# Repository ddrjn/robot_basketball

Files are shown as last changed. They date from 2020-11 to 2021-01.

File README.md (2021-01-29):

stm32 based board design and firmware for robot basketball

Tu run the codes you need processing environment, download from processing.org
 Then add libraries from library manager, only one needed to add is processing.video
Connect camera and stm board. 
Press run. 
One code is for serial communication and keyboard controll.
One is for camera and serial comunication
Last one is for webserver setub and webcontrol of robot.

For mainboard firmware there is main.c file. It is meant for stm cube ide
Configure the stm board as described on wiki and paste the main.c code in there.

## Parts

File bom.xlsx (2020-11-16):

Name | Part Name | Footprint | Quantity | Manufacturer | Supplier | Supplier part ID | Link
reverse voltage protection mosfet | BUK6Y10-30PX | LFPAK56 | 1 | NEXPERIA | fernell | 3438512 | https://ee.farnell.com/nexperia/buk6y10-30px/mosfet-p-ch-30v-80a-lfpak56/dp/3438512?st=buk6y10-30px
zener diode | MMSZ5234BT1G | SOD-123 | 1 |  | fernell | 1431276 | https://ee.farnell.com/on-semiconductor/mmsz5234bt1g/diode-zener-6-2v-0-5w/dp/1431276?st=mmsz5234b
5 v regulator | TPS70950DBVR | SOT-23-5 | 1 |  | fernell | 3122409 | https://ee.farnell.com/texas-instruments/tps70950dbvr/ldo-fixed-0-15a-5v-sot-23-5/dp/3122409?st=tps70950
motor driver | DRV8874QPWPRQ1 |  | 3 |  | mouser | 595-DRV8874QPWPRQ1 | https://www.mouser.ee/ProductDetail/Texas-Instruments/DRV8874QPWPRQ1?qs=mAH9sUMRCttZUT1myh3Itg==
isolator- 16pin | SI8660BB-B-IU | QSOP | 1 | silicon labs | fernell | 3105912 | https://ee.farnell.com/silicon-labs/si8660bb-b-iu/digital-isolator-6ch-40-to-125deg/dp/3105912
isolator 8pin | SI8620BB-B-IS | qsop | 1 | silicon labs | fernell | 2423240 | https://ee.farnell.com/silicon-labs/si8620bb-b-is/digital-isolator-8ns-nsoic-8/dp/2423240
usb connector | 10118193-0001LF | TH | 1 |  | fernell | 2751675 | https://ee.farnell.com/amphenol-icc-fci/10118193-0001lf/micro-usb-2-0-type-b-rcpt-smt/dp/2751675?ost=2751675
esd protection | USBLC6-2SC6 | sot23 | 1 |  | fernell | 1269406 | https://ee.farnell.com/stmicroelectronics/usblc6-2sc6/esd-protection-3-5pf-17v-sot23/dp/1269406?st=usblc6-2sc6
programmer connector | FTSH-105-01-L-DV-K-P | SM | 1 |  | fernell | 2856437 | https://ee.farnell.com/samtec/ftsh-105-01-l-dv-k-p/connector-header-10pos-2row-1/dp/2856437
microprocessor | STM32G431KBT6 | LQFP-32 | 1 | STM | mouser | 511-STM32G431KBT6 | https://www.mouser.ee/ProductDetail/STMicroelectronics/STM32G431KBT6?qs=T3oQrply3y8teCTeNAFOLg%3D%3D | fernell appears to have them only from december
connector for motors | 215079-4 |  | 5 |  | fernell | 1772996 | https://ee.farnell.com/amp-te-connectivity/215079-4/connector-4way-vertical-1-27/dp/1772996
3.3v regulator | TLV70233DBVR | SOT-23-5 | 1 |  | fernell | 3007784 | https://ee.farnell.com/texas-instruments/tlv70233dbvr/ldo-fixed-3-3v-0-3a-sot-23-5/dp/3007784?ost=3007784

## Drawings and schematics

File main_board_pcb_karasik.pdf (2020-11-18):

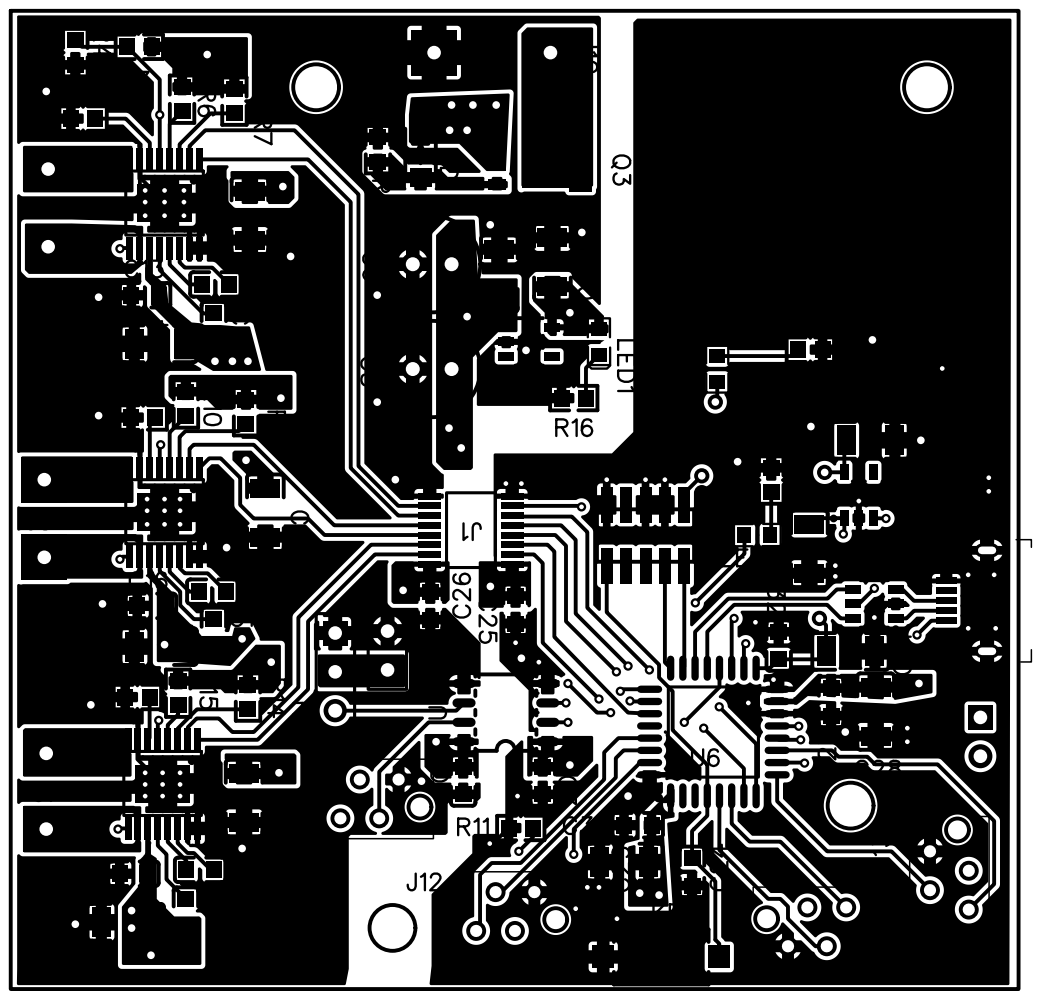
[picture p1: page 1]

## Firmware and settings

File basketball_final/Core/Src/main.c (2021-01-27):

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
/* Includes ------------------------------------------------------------------*/
#include "main.h"
#include "usb_device.h"
#include "usbd_cdc_if.h"
#include "stdio.h"
#include "stdlib.h"
#include "string.h"
#include "Math.h"
/* USER CODE BEGIN Includes */
int tv=0;
/* USER CODE END Includes */

TIM_HandleTypeDef htim1;
TIM_HandleTypeDef htim2;
TIM_HandleTypeDef htim3;
TIM_HandleTypeDef htim8;
TIM_HandleTypeDef htim15;
TIM_HandleTypeDef htim17;

void SystemClock_Config(void);
static void MX_GPIO_Init(void);
static void MX_TIM1_Init(void);
static void MX_TIM2_Init(void);
static void MX_TIM3_Init(void);
static void MX_TIM8_Init(void);
static void MX_TIM15_Init(void);
static void MX_TIM17_Init(void);
/* USER CODE BEGIN 0 */
typedef struct Command { // (1)
  int16_t speed1;
  int16_t speed2;
  int16_t speed3;
  uint16_t throwerSpeed;
  uint16_t delimiter; // (2)
} Command;

typedef struct Feedback { // (3)
  int16_t speed1;
  int16_t speed2;
  int16_t speed3;
  uint16_t delimiter;
} Feedback;

char* rec;

uint8_t usbuf[100];
uint8_t lastlen=100;

Command command = {.speed1 = 0, .speed2 = 0, .speed3 = 0, .throwerSpeed = 0, .delimiter = 0}; // (4)
volatile uint8_t isCommandReceived = 0; // (5)

void CDC_On_Receive(uint8_t* buffer, uint32_t* length) { // (6)
  //if (*length == sizeof(Command)) { // (7)
	uint8_t len1=(uint8_t) *length;
	lastlen=len1;
	memset(usbuf, "\0",100);
   memcpy(usbuf, buffer, len1);
	memset(buffer, "\0",100);
   // (8)
    //memcpy(&rec, buffer, 200);
   // if (command.delimiter == 43690) { // (9)
      isCommandReceived = 1;
   // }
 //}
}




uint8_t ret[9][5];
int m2s=0;
uint16_t values[9];
//m1speed,m2speed,m3speed,m1dir,m2dir,m3dir,servo1,servo2,esc


void splitm(uint8_t* msg){

  for (int i=0;i<9;i++){

      values[i]=0;

  }


int count=0;
int mpov=-1;


  for (int i=0;i<lastlen;i++){


    if(msg[i]==';'){int mpov1=mpov;
      while(mpov!=-1){
        values[count]+=(ret[count][mpov1-mpov]-48)*pow(10,mpov);
        mpov--;


      }

      count++; mpov=-1;}

    else{


      mpov++;
      ret[count][mpov]=msg[i];

    }



//    if(msg[i]==';'){ret[0]=10;break;}
//    if(msg[i]==','){ret[0]=50;break;}
//    if(msg[i]==':'){ret[0]=100;break;}
//    if(msg[i]=='|'){ret[0]=0;break;}

  }









}





uint16_t fdbck;



/* USER CODE END 0 */

/**
  * @brief  The application entry point.
  * @retval int
  */
int main(void)
{
  /* MCU Configuration--------------------------------------------------------*/

  /* Reset of all peripherals, Initializes the Flash interface and the Systick. */
  HAL_Init();

  /* Configure the system clock */
  SystemClock_Config();

  /* Initialize all configured peripherals */
  MX_GPIO_Init();
  MX_USB_Device_Init();
  MX_TIM1_Init();
  MX_TIM2_Init();
  MX_TIM3_Init();
  MX_TIM8_Init();
  MX_TIM15_Init();
  MX_TIM17_Init();
  /* Infinite loop */
  /* USER CODE BEGIN WHILE */


  MX_TIM15_Init();//m1en and m2en
  MX_TIM8_Init();//m3en

  MX_TIM3_Init();//servo2 channel 2
  HAL_TIM_PWM_Start(&htim15, TIM_CHANNEL_2);//m1
  HAL_TIM_PWM_Start(&htim15, TIM_CHANNEL_1);//m2
  HAL_TIM_PWM_Start(&htim8, TIM_CHANNEL_1);//m3
  HAL_TIM_PWM_Start(&htim3, TIM_CHANNEL_2);//servo
  HAL_TIM_PWM_Start(&htim2, TIM_CHANNEL_4);//esc
  HAL_TIM_PWM_Start(&htim3, TIM_CHANNEL_3);//esc


  HAL_GPIO_WritePin(GPIOA, GPIO_PIN_9, GPIO_PIN_SET);
  HAL_GPIO_WritePin(GPIOA, GPIO_PIN_5, GPIO_PIN_SET);
  HAL_GPIO_WritePin(GPIOB, GPIO_PIN_4, GPIO_PIN_SET);






  while (1)
  {
    /* USER CODE END WHILE */

    /* USER CODE BEGIN 3 */


	  if (isCommandReceived) { // (2)
	        isCommandReceived = 0;
	        HAL_GPIO_TogglePin(GPIOB,GPIO_PIN_3); // (3)



	      splitm(usbuf);//allocate values sent from pc to values variable

	      //phase of M1
	      if(values[3]==1)HAL_GPIO_WritePin(GPIOA, GPIO_PIN_9, GPIO_PIN_SET);
	      	  	  else if(values[3]==0)GPIOA -> ODR &= ~GPIO_PIN_9;
	      //phase of M2
	      if(values[4]==1)HAL_GPIO_WritePin(GPIOA, GPIO_PIN_5, GPIO_PIN_SET);
	     	      else if(values[4]==0)GPIOA -> ODR &= ~GPIO_PIN_5;
	      //phase of M3
	      if(values[5]==1)HAL_GPIO_WritePin(GPIOB, M3PH_Pin, GPIO_PIN_SET);
	     	      else if(values[5]==0)GPIOB -> ODR &= ~M3PH_Pin;




	        TIM15->CCR2 = values[0];//M1EN
	          TIM15->CCR1 = values[1];//M2En
	          TIM8->CCR1 = values[2];//M3EN





              //11111;11111;11111;1;1;1;1000;1000;99999 test transmition
//servo and esc receive values from 0-10000, motors from 0 - 65535
int servod=values[6];
servod=(int)servod/1.574;
servod=servod+1640;

	TIM3->CCR2 = servod;//servo2





int escs=values[7];
if(escs!=0){
escs=(int)escs/3.335;
escs=escs+3500;

//
TIM2->CCR4 = escs;//esc
	TIM3->CCR3 = escs;//esc


}

	       //CDC_Transmit_FS(values, sizeof(values)); // (5)

	      }

  }
  /* USER CODE END 3 */
}

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


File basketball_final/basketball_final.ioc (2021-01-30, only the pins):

Mcu.UserName=STM32G431KBTx
PA10.Signal=S_TIM2_CH4
PA11.Signal=USB_DM
PA12.Signal=USB_DP
PA13.Signal=SYS_JTMS-SWDIO
PA14.Signal=SYS_JTCK-SWCLK
PA15.GPIO_Label=TIM8_CH1_M3EN
PA15.Signal=S_TIM8_CH1
PA2.GPIO_Label=TIM15_CH1_M2EN
PA2.Signal=S_TIM15_CH1
PA3.GPIO_Label=TIM15_CH2_M1EN
PA3.Signal=S_TIM15_CH2
PA5.GPIO_Label=M2PH
PA5.Signal=GPIO_Output
PA7.Signal=S_TIM3_CH2
PA8.GPIO_Label=TIM1_CH1_SERVO1
PA8.Signal=S_TIM1_CH1
PA9.GPIO_Label=M1PH
PA9.Signal=GPIO_Output
PB0.Signal=S_TIM3_CH3
PB3.GPIO_Label=MCU_LED
PB3.Signal=GPIO_Output
PB4.GPIO_Label=M3PH
PB4.Signal=GPIO_Output

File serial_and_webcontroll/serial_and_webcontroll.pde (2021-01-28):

/**
 * Simple Write. 
 * 
 * Check if the mouse is over a rectangle and writes the status to the serial port. 
 * This example works with the Wiring / Arduino program that follows below.
 */


import processing.serial.*;
import processing.net.*;

Server s;
Client c;
Serial myPort;  // Create object from Serial class
int val;        // Data received from the serial port
int s1,s2,s3,d1,d2,d3,servo,esc;
int data[];
void setup() 
{
  size(200, 200);
  // I know that the first port in the serial list on my mac
  // is always my  FTDI adaptor, so I open Serial.list()[0].
  // On Windows machines, this generally opens COM1.
  // Open whatever port is the one you're using.
  String portName = Serial.list()[0];
  myPort = new Serial(this, portName, 115200);
  s = new Server(this, 12345);
  s1=1000;
  s2=1000;
  d3=1;

}

void draw() {
  background(255);
 
       c = s.available();
  if (c != null) {
    String input = c.readString();
    input = input.substring(0, input.indexOf("\n")); // Only up to the newline
    data = int(split(input, ',')); // Split values into an array
    // Draw line using received coords
   s1=data[0];
    s2=data[1];
     s3=data[2];
      d1=data[3];
    d2=data[4];
     d3=data[5];
      servo=data[6];
   esc=data[7];
   
       
  myPort.write(generateMessage()); 
     
   
   
  }
      
      
      
      
      

}


void mousePressed(){
  
  //moveF(10000);
  //turn(1,10000);
}


void keyPressed(){
  
 if(key=='w'){
 moveF(40000,1);
 
 } 
   if(key=='a'){
turn(1,10000);
 
 } 
    if(key=='d'){
turn(0,10000);
 
 } 
  
      if(key=='s'){
moveF(10000,0);
 
 } 
  
  
}


void keyReleased(){
  
  
 stopM(); 
  
}
void mouseReleased(){
  
 stopM(); 
  //turn(0,20000);
  
}

void moveF(int speed,int dir){
  d1=0;
  d2=1;
  if(dir==0){d1=1;d2=0;}
  
  s3=0;
  s1=speed;
  s2=speed;
  
  
  
  
  
  myPort.write(generateMessage());     
  
  
  
}


void stopM(){
s1=0;
s2=0;
s3=0;

 myPort.write(generateMessage());     

}


void turn(int dir,int speed){
  if (dir==1){
   d1=1;
   d2=1;
   d3=1;
    
    
  }
  else {
     d1=0;
   d2=0;
   d3=0;
   
  }
  s1=speed;
  s2=speed;
  s3=speed;
  
  
  myPort.write(generateMessage());     
  
  
  
  
}


String generateMessage(){
  
  
  
 String out="";
 out+=str(s1);
 out+=";";
  out+=str(s2);
 out+=";";
  out+=str(s3);
 out+=";";
  out+=str(d1);
 out+=";";
  out+=str(d2);
 out+=";";
  out+=str(d3);
 out+=";";
  out+=str(servo);
 out+=";";
  out+=str(esc);
   out+=";";
  out+=str(99999);
 
 return out;
  
  
}

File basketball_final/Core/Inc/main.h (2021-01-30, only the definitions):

#define TIM15_CH1_M2EN_Pin GPIO_PIN_2
#define TIM15_CH1_M2EN_GPIO_Port GPIOA
#define TIM15_CH2_M1EN_Pin GPIO_PIN_3
#define TIM15_CH2_M1EN_GPIO_Port GPIOA
#define M2PH_Pin GPIO_PIN_5
#define M2PH_GPIO_Port GPIOA
#define TIM1_CH1_SERVO1_Pin GPIO_PIN_8
#define TIM1_CH1_SERVO1_GPIO_Port GPIOA
#define M1PH_Pin GPIO_PIN_9
#define M1PH_GPIO_Port GPIOA
#define TIM8_CH1_M3EN_Pin GPIO_PIN_15
#define TIM8_CH1_M3EN_GPIO_Port GPIOA
#define MCU_LED_Pin GPIO_PIN_3
#define MCU_LED_GPIO_Port GPIOB
#define M3PH_Pin GPIO_PIN_4
#define M3PH_GPIO_Port GPIOB

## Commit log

2020-10-02 added schematics for checking
    [BOM_basketball main board_2020-10-02_16-46-45.csv, Sheet_1_2020-10-02_16-46-16.schdoc, components.xlsx]
2020-10-09 fixed all the issues , update for checking.
    [main_board gen 2.csv, main_board gen 2.schdoc]
2020-10-14 added pcb design gerber
2020-10-14 pcb layout for main board.
2020-10-20 Add files via upload
    pcb layout 2.0
2020-11-03 gen 3 of pcb layout
2020-11-13 gen 8 pcb design
2020-11-16 ordering list
    [bom.xlsx]
2020-11-18 final round of fixes(I hope) with gerber files
    [bom.xlsx]
2020-11-18 removed empty folder
    [bom.xlsx]
2021-01-27 firmware of main board

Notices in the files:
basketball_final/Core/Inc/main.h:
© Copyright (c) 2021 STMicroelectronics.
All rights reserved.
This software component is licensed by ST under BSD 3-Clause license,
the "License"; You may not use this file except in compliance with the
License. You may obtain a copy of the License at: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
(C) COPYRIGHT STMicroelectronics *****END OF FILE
